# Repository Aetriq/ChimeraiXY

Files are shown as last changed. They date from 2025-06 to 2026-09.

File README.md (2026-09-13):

# Chimera iXY - CoreXY Build

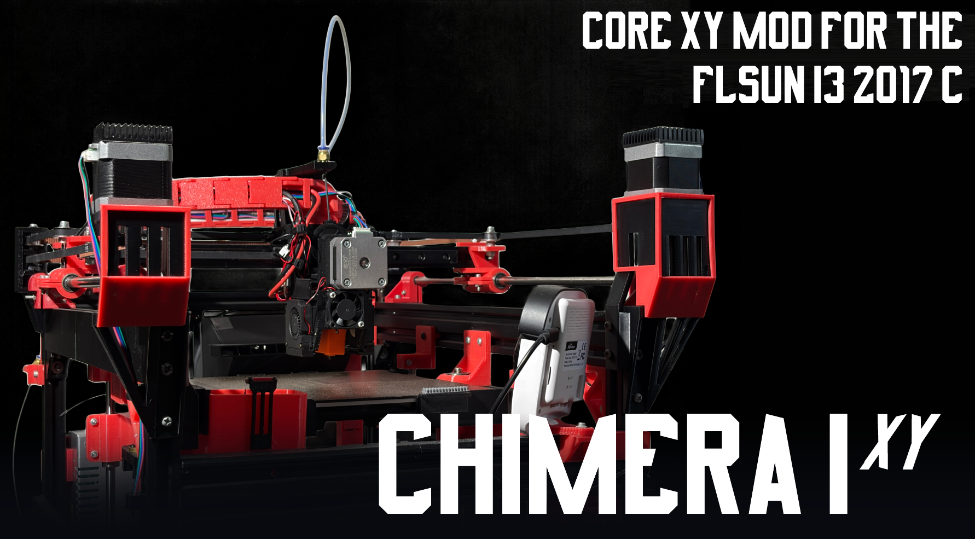
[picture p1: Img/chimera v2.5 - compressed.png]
Banner 1

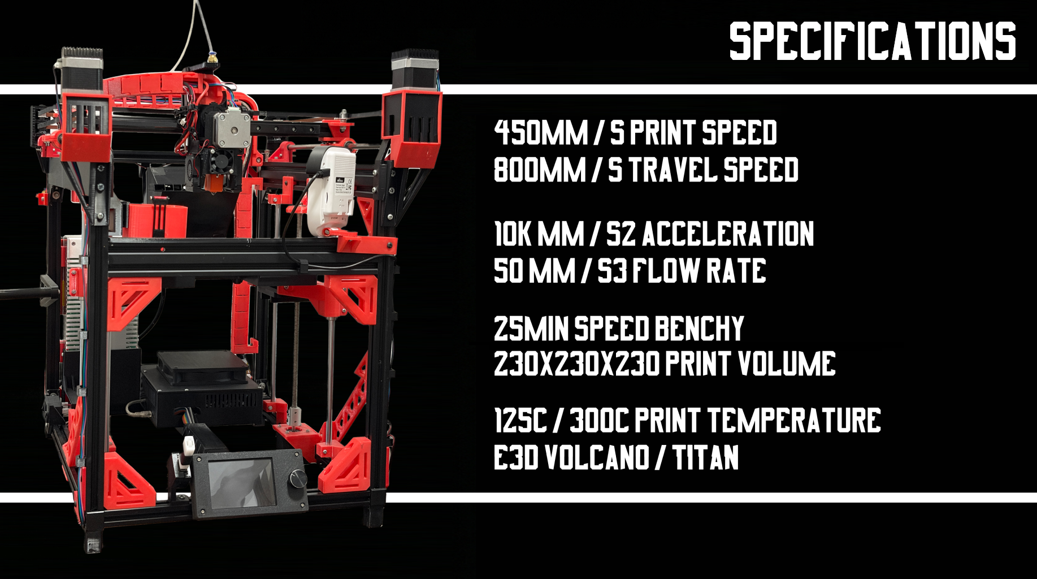
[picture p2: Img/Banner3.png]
Banner 2


A DIY CoreXY conversion of the Flsun i3 2017 3D printer. This project includes firmware and relevant 3D model files for the custom build. A Mingda Magician X with a burnt out mainboard and 20-pin ribbon cable was also used in this build. I chose the name 'Chimera' since this printer is essentially two completely different 3D printers with a ~5 year gap combined together to make a hybrid printer.

This is not only to demonstrate the ability of upcycling reprap in conjunction with modern printers, but also to prove that only linear rods, bearings and extrusions are needed to make a fast printer that rivals high end consumer printers while being at a lower cost.

**What's the objective of this project?** My main objective is not to make an insanely fast 3D printer, anything above 200mm/s is the goal with speeds near 500mm/s in mind. Instead, I wanted to make this printer as reliable as possible, moreso than the two bedslingers it was made out of. The Flsun (While a good printer for its time) is obviously last gen, so it's quite finicky to get quality models by today's standards, and the MMX was simply made out of cheap parts that probably didn't even pass QoS (there's also alot of review online of mingda printers using parts with questionable quality). This printer will primarily be used to build large electronic enclosures. 

**LATEST UPDATE LOG (v2.4):** - Added a nozzle cleaning system, including a ptfe wiper and nozzle brush. Partially inspired by the system seen on bambu's a1 series, this system works very well and the klipper config has been updated accordingly.
- Added an auxillary cooling fan, a 120x25mm axial 150CFM fan. This should've been a centrifugal blower but I had this one on hand and it pushes a decent amount of H20 pressure.
- Quality of life improvements to firmware, including the implementation of above. Thermal testing of steppers made me stay at 1.2A RMS for X and Y motors.

## Overview of Specifications

- **Firmware**: Klipper & MainsailOS. Marlin 2.1.2.5 continues to be supported.  
- **Controller Board**: Supports MKS Gen L vX.X, TinyBee vX.X, and Robin Nano v3.X.*
- **Build Type**: CoreXY mechanical configuration
- **Speed**: Quality Prints @ 300mm/s. Travel speeds up to 800mm/s.
- **Accel**: Up to 20k mm/s*s accel
- **Drivers**: Minimum TMC2209 UART required (>2.0A peak)
- **Build Volume**: 230mm^3
- **Extrusion**: E3D Titan Extruder Direct Drive or Bowden.
- **Hotend**: V6 volcano or normal w/ all-metal heatbreak. Supports PLA, PETG, ABS, ASA, TPU (>72D)

**Due to unforeseen circumstances, I have changed to the Robin Nano v3.1.* ### Experimental Results
Below is a comparison of the donor hardware versus the theoretical goals and final experimental data. In conclusion, alot of my project goals were met and even exceeded in some cases!

| Specification | Flsun i3 (Donor 1) | Mingda Magician X (Donor 2) | Planned Theoretical Goal | Experimental Results |
| :--- | :--- | :--- | :--- | :--- |
| **Max Print Speed** | ~100 mm/s | ~80-120 mm/s | 200-500 mm/s | 200-450mm/s|
| **Max Travel Speed** | ~150 mm/s | ~200 mm/s | 500+ mm/s | 800mm/s |
| **Max Acceleration** | ~1000 mm/s² | ~1500 mm/s² | 20000 mm/s² | 32000 mm/s² (according to input shaping)|
| **Volumetric Flow Rate** | ~8 mm³/s | ~10-12 mm³/s | >20 mm³/s | 40 mm³/s|
| **Build Volume** | 220x220x220 mm | 230x230x260 mm | 230x230x230 mm | 230x230x230 mm|
| **Kinematics** | Cartesian | Cartesian | CoreXY | CoreXY |

## Links

- [Official Page](https://aetriq.xyz/chimera.html)
- [Wiki Page](https://github.com/Aetriq/ChimeraiXY/wiki/Wiki-Page-%E2%80%90-Chimera-iXY-v2.0)
- [Full Documentation](https://aetriq.xyz/chimeradocfull.html)
- [Bill of Materials](https://aetriq.xyz/chimeradocfull.html#bom)

## Contents

- `Firmware - Mainboard/` – Klipper & Marlin 2.1.2.5 configuration for MKS Robin Nano v3.1. 
- `Firmware - ESP8266/` – Configuration for MKS Wifi v1.0. Only used in Marlin Build. 
- `Config/` - Slicer Profiles, Bootscreen, etc.
- `Model/` – 3D printable parts for CoreXY conversion (mounts, brackets, etc.)  
- `Doc/` – Rough Concept Sketches, Torque Curves, and printer setup details
- `Img/` – Images featured here, as well as some diagrams

## Configuration
Refer to config folder for start gcode for marlin, or firmware for klipper start/end gcode. This printer works optimally on both superslicer or prusaslicer but supports any marlin flavored gcode.

## Model Credits
Credits to the following models for making this possible. Please check them out:

- [1] 20 x 20 mm extrusion Power Source Unit (PSU) mount bracket – [[source/link](https://www.printables.com/model/457450-20-x-20-mm-extrusion-power-source-unit-psu-mount-b/files)]  
- [2] Bowden / PTFE Tube Coupler - Connect 2 Tubes – [[source/link](https://makerworld.com/en/models/664607-bowden-ptfe-tube-coupler-connect-2-tubes#profileId-591977)]  
- [3] E3D v6 dual 4010 fan duct – [[source/link](https://www.printables.com/model/239901-e3d-v6-dual-4010-fan-duct/files)]  
- [4] the100: 8mm linear rod gantry - [[source/link](https://github.com/MSzturc/the100/tree/main/STL/Gantry)]
- [5] KP3S PSU 120mm fan adapter (ZL-360-24) - [[source/link](https://www.thingiverse.com/thing:6010144)]
- [6] Case for Makerbase MKS TS35 V2.0 touchscreen - [[source/link](https://www.printables.com/model/83429-case-for-makerbase-mks-ts35-v20-touchscreen/comments)]
- [7] Drag Cable Chain(s) - [[source/link](https://www.printables.com/model/34894-drag-cable-chains/files)]
- [8] Modification pack, Ender 5 plus, KAY3D CoreXY. - [[source/link](https://www.thingiverse.com/thing:4643208/files)]

## Software Credits
- [1] Autodesk Fusion [[source/link](https://www.autodesk.com/products/fusion-360/personal)]
- [2] PrusaSlicer [[source/link](https://www.prusa3d.com/page/prusaslicer_424/)]
- [3] SuperSlicer [[source/link](https://superslicer.net/)]
- [4] Klipper [[source/link](https://www.klipper3d.org/)]
- [5] Configuration for MKS TS35 V2.0 working with klipper screen [[source/link](https://github.com/NamkingWIN/3d_print/wiki/Configuration-for-MKS-TS35-V2.0-working-with-klipper-screen)]
- [6] StepperSim [[source/link](https://github.com/rcarlyle/StepperSim)]

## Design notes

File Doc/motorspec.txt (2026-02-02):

42SHDC4023Z-23B

- 17 Stepper
- 42 Motor
- Step angle: 1.8 degree
- Number of phases: 2
- Voltage: DC 2.55V
- Current: 1.5A/phase
- Resistance: 4.4 ohm
- Holding torque: 2420 mN.m
- Positioning torque : 20mN.m REF

 42BYGH439-B-20D
- 17 Stepper
- 42 Motor
- Step angle: Likely 0.9 degree
- Number of phases: 2
- Voltage: DC 2.55V
- Current: 1.7A/Phase
- Resistance: 1.5-1.8 ohm
- Holding torque: ~40 - 45 N.cm

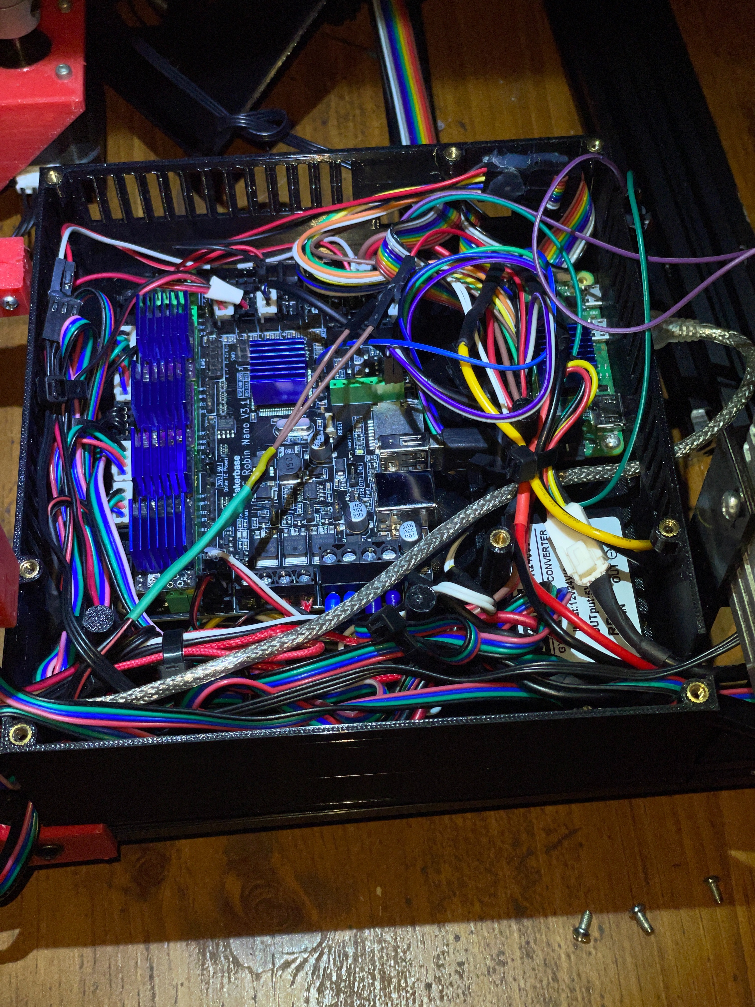
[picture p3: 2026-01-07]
Img/Primary Electronics Case.JPG

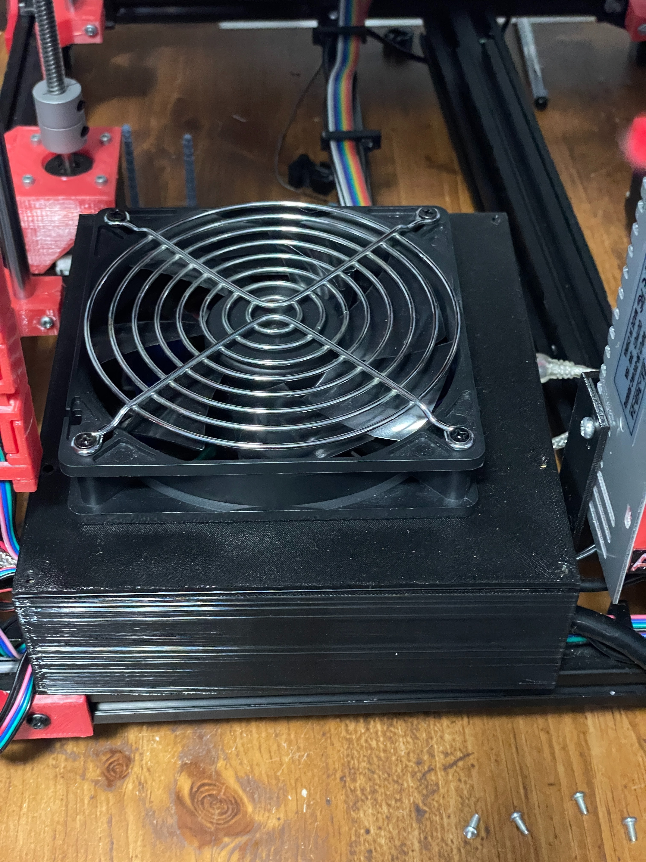
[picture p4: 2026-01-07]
Img/Primary Electronics Case Closed.JPG

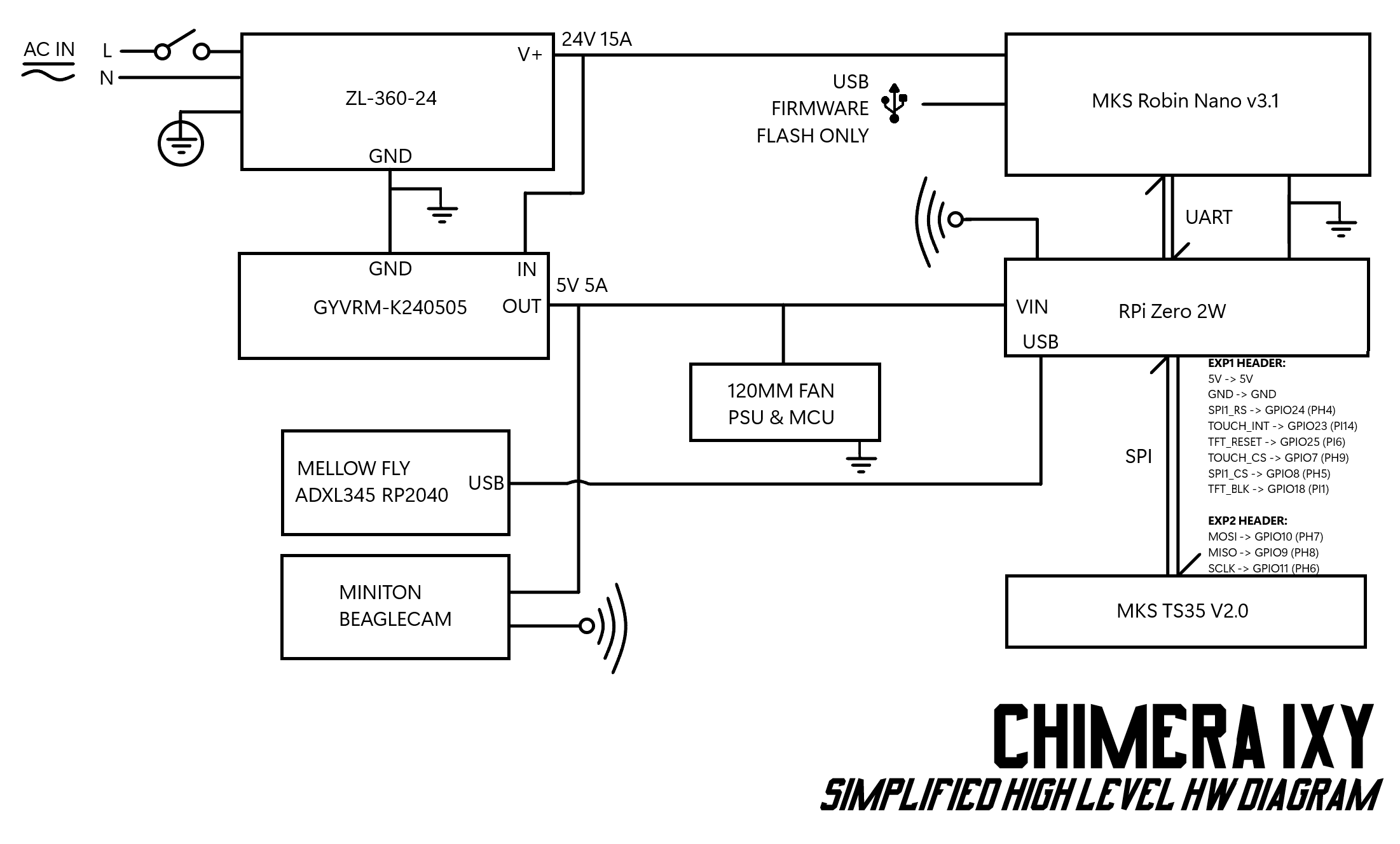
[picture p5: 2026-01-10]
Doc/Simplified Hardware Diagram.png

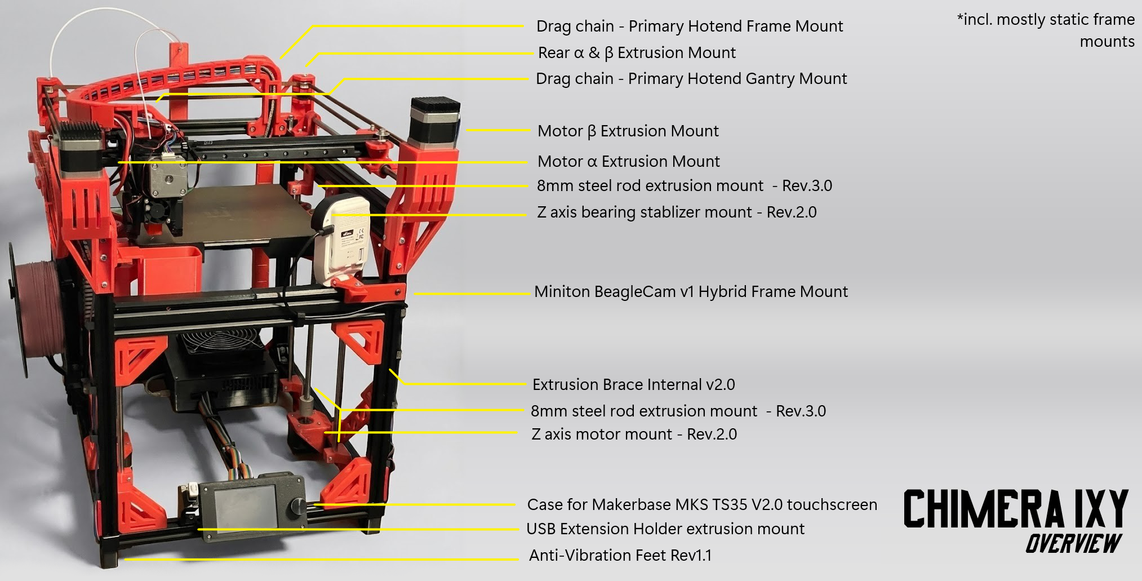
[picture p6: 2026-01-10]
Doc/Overview v2.0.png

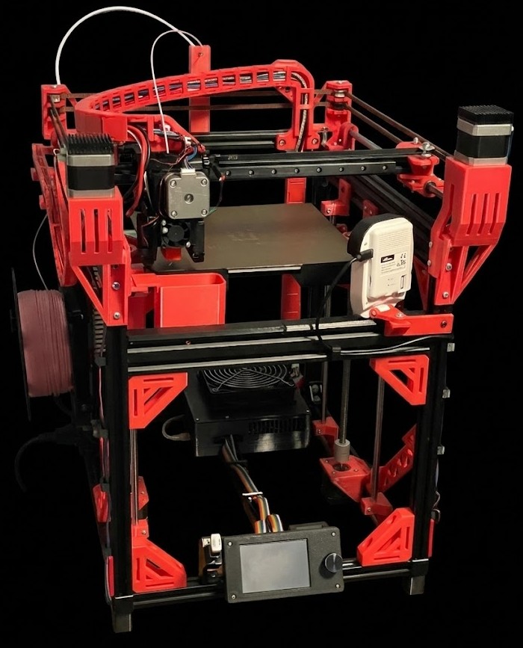
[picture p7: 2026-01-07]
Img/v2.0.jpg

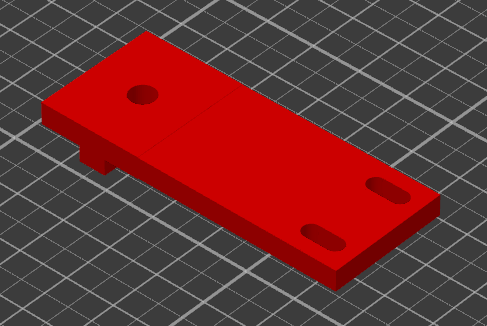
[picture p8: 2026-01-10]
Img/thumb/Y axis endstop switch Frame Mount.png

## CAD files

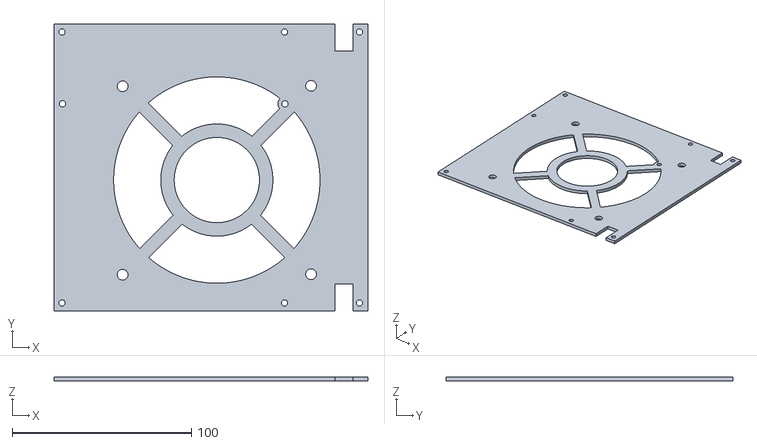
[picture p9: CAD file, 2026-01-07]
Model/Electronics/Primary Case - Top Cover.stl
175.0 x 160.0 x 2.50

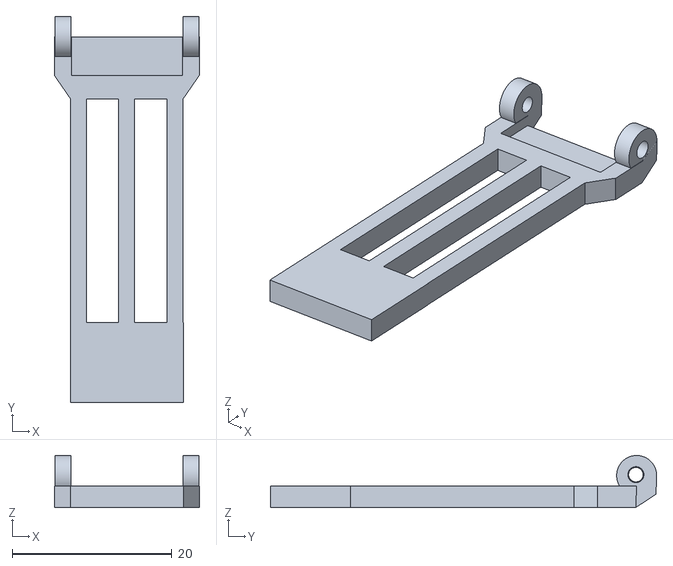
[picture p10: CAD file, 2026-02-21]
Model/etc/Glue-on PTFE Nozzle Wiper.stl
18.1 x 48.3 x 6.51

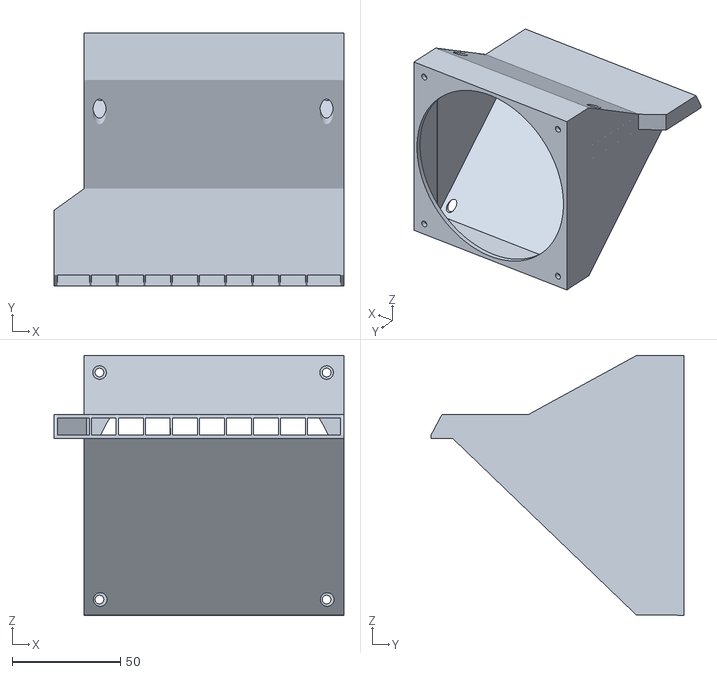
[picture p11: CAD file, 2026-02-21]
Model/Frame Mounts/Auxillary Bed Cooling Fan Mount (120mm Axial, mirror other side) (2).stl
134.1 x 117.0 x 120.3

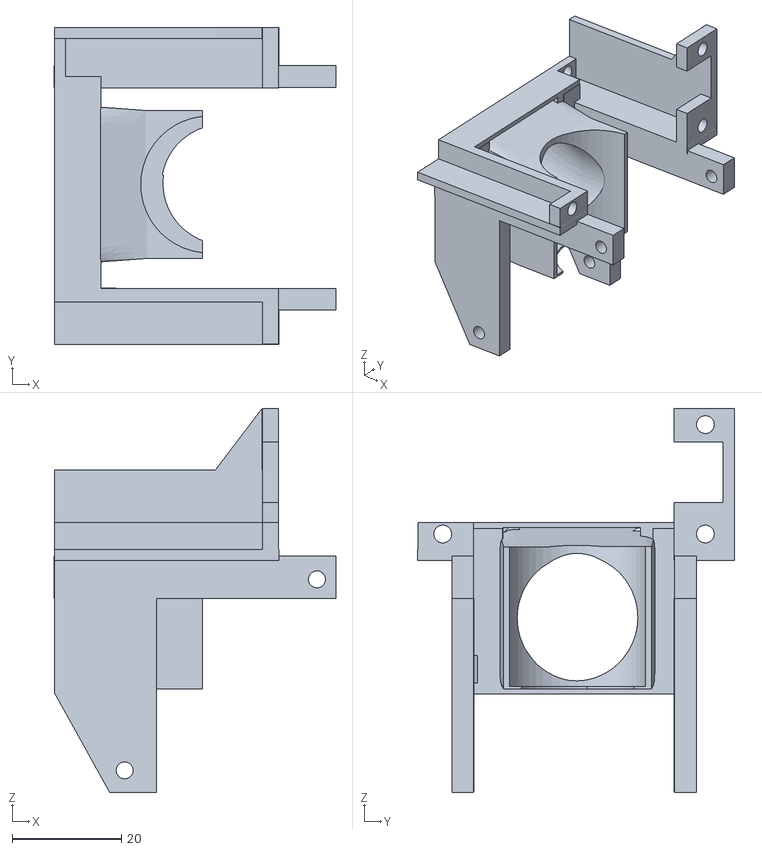
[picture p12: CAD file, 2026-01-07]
Model/Gantry/Mounting Bracket - Fans.stl
51.5 x 57.9 x 70.2

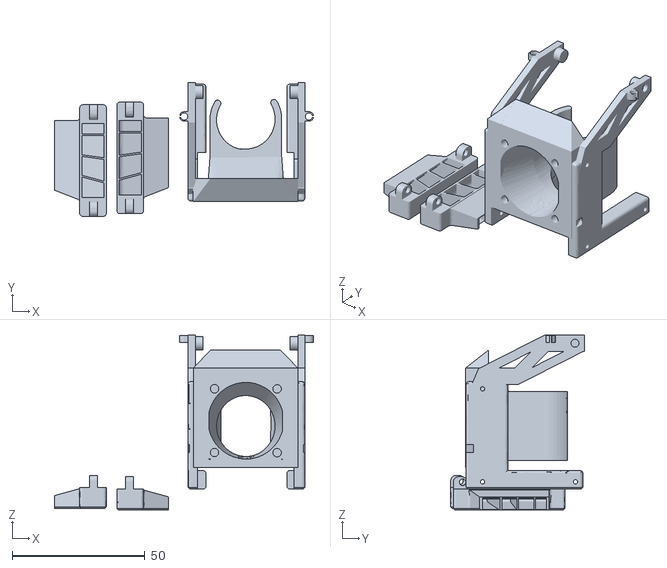
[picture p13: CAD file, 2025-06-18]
Model/Hotend/Hotend 30mm + 4010x2 Shroud.stl
97.5 x 50.3 x 65.7

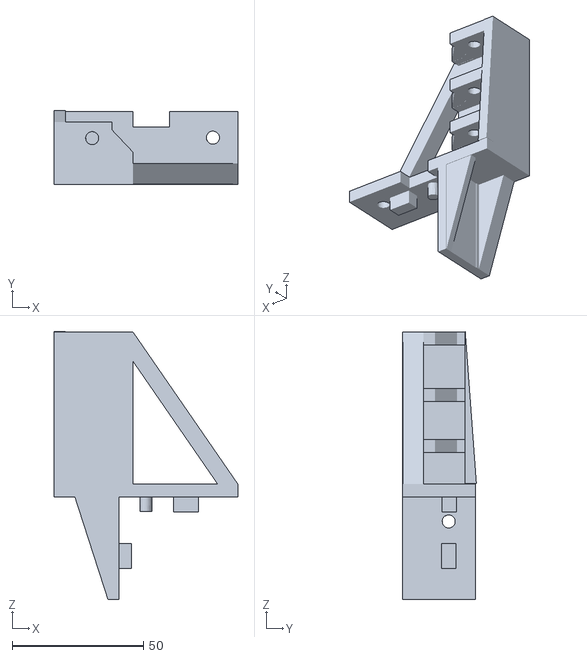
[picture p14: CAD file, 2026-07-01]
Model/Kinematics/Rear α & β Extrusion Mount (Right side, mirror model on y for left side) v2.5.stl
70.0 x 28.1 x 102.1

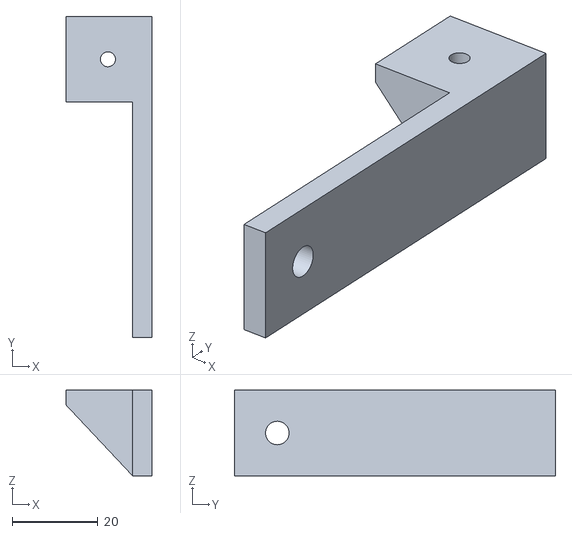
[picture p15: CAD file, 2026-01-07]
Model/Electronics/Miniton BeagleCam v1 Hybrid Frame Mount.stl
20.0 x 75.0 x 20.0

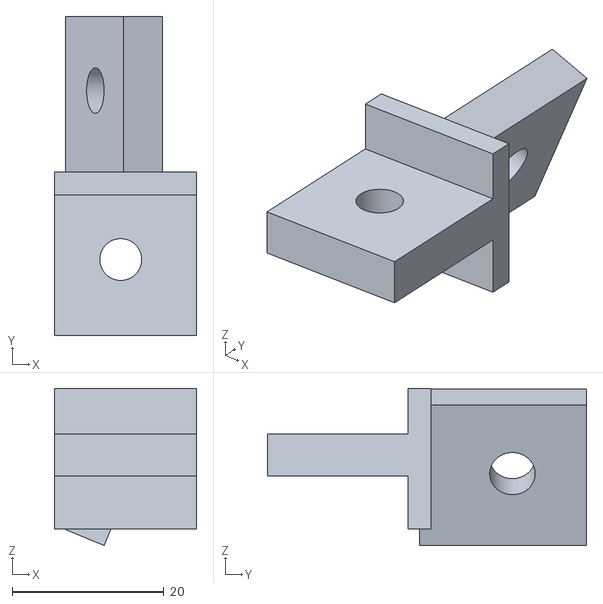
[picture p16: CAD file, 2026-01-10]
Model/etc/Filament Guide - Bottom.stl
18.8 x 42.0 x 20.7

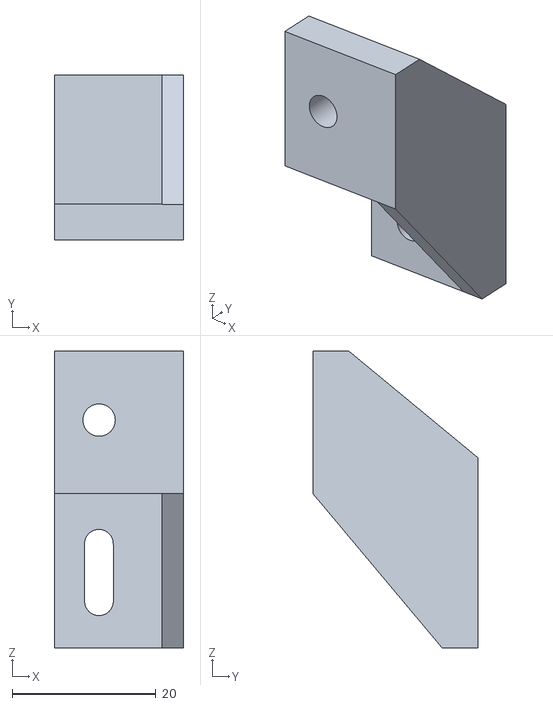
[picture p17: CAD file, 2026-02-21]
Model/Frame Mounts/Auxillary Bed Cooling Fan Mount (120mm Axial, mirror other side) (1).stl
18.0 x 23.0 x 41.4

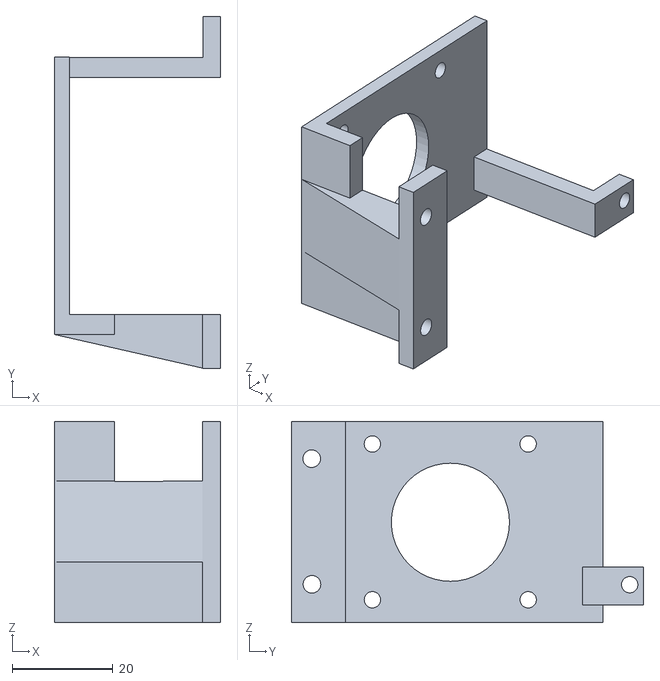
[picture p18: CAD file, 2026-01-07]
Model/Gantry/Mounting Bracket - Extruder & Hotend.stl
33.1 x 70.1 x 40.0

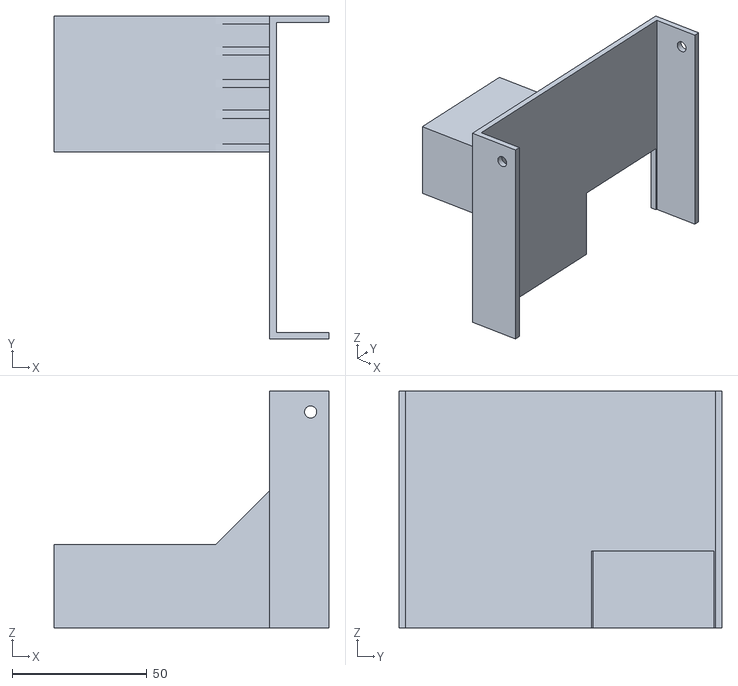
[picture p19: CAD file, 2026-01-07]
Model/Electronics/Power Supply Cover.stl
102.0 x 120.0 x 88.0

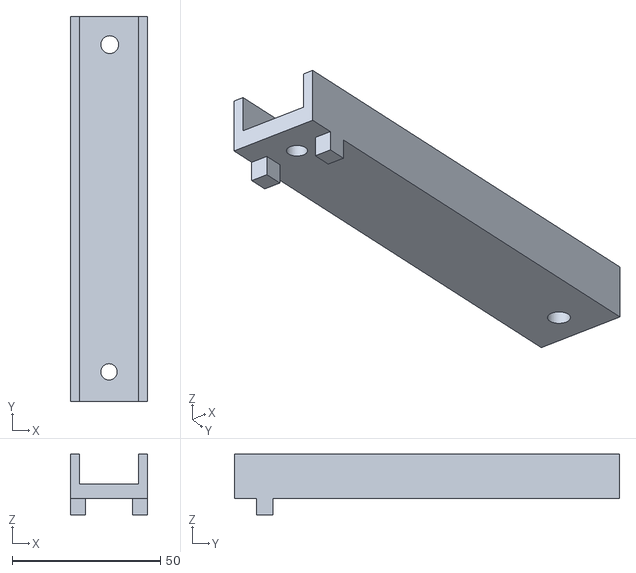
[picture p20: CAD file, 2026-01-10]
Model/etc/Filament Guide - Top.stl
26.0 x 130.0 x 20.5

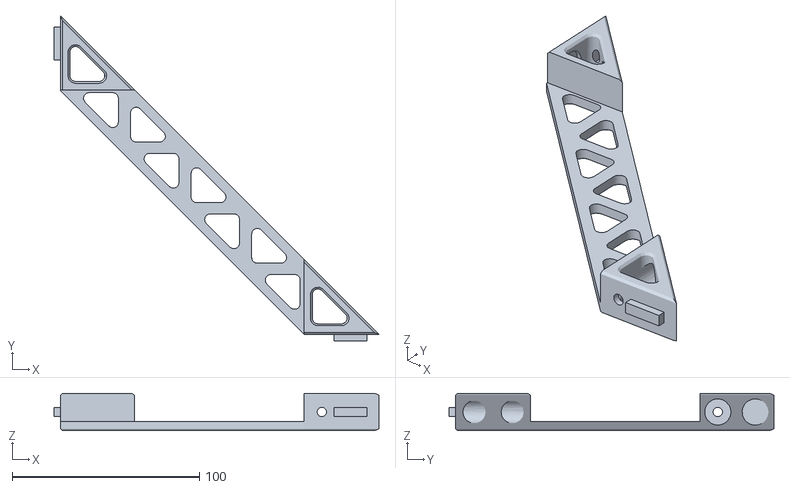
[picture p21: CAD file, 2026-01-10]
Model/Frame Mounts/Extrusion Brace Internal Long.stl
173.5 x 173.5 x 20.0

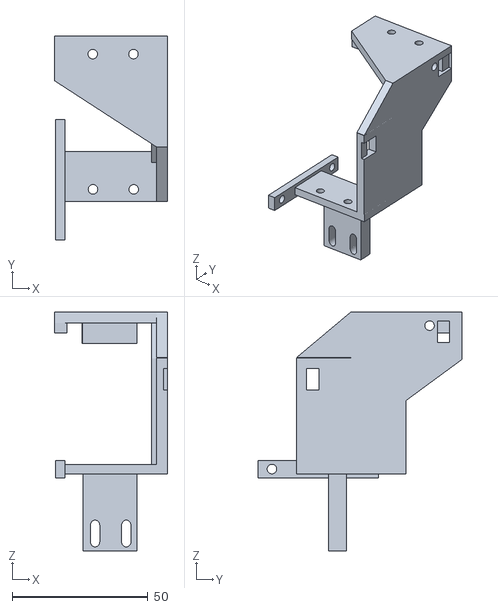
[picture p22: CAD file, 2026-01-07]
Model/Gantry/Back Gantry Plate.stl
41.7 x 75.0 x 87.9

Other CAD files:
Model/Electronics/Primary Case - Bottom.stl
Model/etc/Filament Spool Holder v2.0 Part 1.stl
Model/Frame Mounts/8mm steel rod extrusion mount (Z-axis, Bottom & Top) - Rev.3.0.stl
Model/Gantry/4010 Shroud.stl
Model/Electronics/MKS TFT35 v2.0 Extrusion Mount (Modified).stl
Model/Frame Mounts/15mm square tube cable clip (Epoxy Mounted).stl
Model/Frame Mounts/15mm square tube extrusion mount.stl
Model/Frame Mounts/30mm height psu support.stl
Model/Frame Mounts/8mm steel rod extrusion mount (OLD).stl
Model/Frame Mounts/8mm steel rod extrusion mount (Y-axis) - Rev.1.0.stl
Model/Frame Mounts/AC Plug + Power Switch extrusion mount.stl
Model/Frame Mounts/Anti-Vibration Feet Rev1.1.stl
Model/Frame Mounts/Cable guide extrusion mount (OLD).stl
Model/Frame Mounts/Cable guide extrusion mount.stl
Model/Frame Mounts/Drag chain - Auxillary Rear Spine Mount.stl
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

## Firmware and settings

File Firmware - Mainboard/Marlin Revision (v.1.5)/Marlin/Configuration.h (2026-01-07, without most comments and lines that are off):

#pragma once
#define CONFIGURATION_H_VERSION 02010205
#define STRING_CONFIG_H_AUTHOR "(none, default config)" // Who made the changes.
#define SHOW_BOOTSCREEN
  #define MOTHERBOARD BOARD_MKS_ROBIN_NANO_V3
#define SERIAL_PORT -1
#define BAUDRATE 250000
#define CUSTOM_MACHINE_NAME "Chimera iXY"
#define X_DRIVER_TYPE  TMC2209
#define Y_DRIVER_TYPE  TMC2209
#define Z_DRIVER_TYPE  TMC2209_STANDALONE
#define E0_DRIVER_TYPE TMC2209_STANDALONE
#define EXTRUDERS 1
#define DEFAULT_NOMINAL_FILAMENT_DIA 1.75
#define TEMP_SENSOR_0 1
#define TEMP_SENSOR_1 0
#define TEMP_SENSOR_2 0
#define TEMP_SENSOR_3 0
#define TEMP_SENSOR_4 0
#define TEMP_SENSOR_5 0
#define TEMP_SENSOR_6 0
#define TEMP_SENSOR_7 0
#define TEMP_SENSOR_BED 1
#define TEMP_SENSOR_PROBE 0
#define TEMP_SENSOR_CHAMBER 0
#define TEMP_SENSOR_COOLER 0
#define TEMP_SENSOR_BOARD 0
#define TEMP_SENSOR_REDUNDANT 0
#define DUMMY_THERMISTOR_998_VALUE  25
#define DUMMY_THERMISTOR_999_VALUE 100
#if TEMP_SENSOR_IS_MAX_TC(0)
  #define MAX31865_SENSOR_OHMS_0      100 // (Ω) Typically 100 or 1000 (PT100 or PT1000)
  #define MAX31865_CALIBRATION_OHMS_0 430 // (Ω) Typically 430 for Adafruit PT100; 4300 for Adafruit PT1000
#endif
#if TEMP_SENSOR_IS_MAX_TC(1)
  #define MAX31865_SENSOR_OHMS_1      100
  #define MAX31865_CALIBRATION_OHMS_1 430
#endif
#if TEMP_SENSOR_IS_MAX_TC(2)
  #define MAX31865_SENSOR_OHMS_2      100
  #define MAX31865_CALIBRATION_OHMS_2 430
#endif
#if HAS_E_TEMP_SENSOR
  #define TEMP_RESIDENCY_TIME         5  // (seconds) Time to wait for hotend to "settle" in M109
  #define TEMP_WINDOW                  1  // (°C) Temperature proximity for the "temperature reached" timer
  #define TEMP_HYSTERESIS              3  // (°C) Temperature proximity considered "close enough" to the target
#endif
#if TEMP_SENSOR_BED
  #define TEMP_BED_RESIDENCY_TIME     5  // (seconds) Time to wait for bed to "settle" in M190
  #define TEMP_BED_WINDOW              1  // (°C) Temperature proximity for the "temperature reached" timer
  #define TEMP_BED_HYSTERESIS          3  // (°C) Temperature proximity considered "close enough" to the target
#endif
#if TEMP_SENSOR_CHAMBER
  #define TEMP_CHAMBER_RESIDENCY_TIME 10  // (seconds) Time to wait for chamber to "settle" in M191
  #define TEMP_CHAMBER_WINDOW          1  // (°C) Temperature proximity for the "temperature reached" timer
  #define TEMP_CHAMBER_HYSTERESIS      3  // (°C) Temperature proximity considered "close enough" to the target
#endif
#if TEMP_SENSOR_REDUNDANT
  #define TEMP_SENSOR_REDUNDANT_SOURCE    E1  // The sensor that will provide the redundant reading.
  #define TEMP_SENSOR_REDUNDANT_TARGET    E0  // The sensor that we are providing a redundant reading for.
  #define TEMP_SENSOR_REDUNDANT_MAX_DIFF  10  // (°C) Temperature difference that will trigger a print abort.
#endif
#define HEATER_0_MINTEMP   5
#define HEATER_1_MINTEMP   5
#define HEATER_2_MINTEMP   5
#define HEATER_3_MINTEMP   5
#define HEATER_4_MINTEMP   5
#define HEATER_5_MINTEMP   5
#define HEATER_6_MINTEMP   5
#define HEATER_7_MINTEMP   5
#define BED_MINTEMP        5
#define CHAMBER_MINTEMP    5
#define HEATER_0_MAXTEMP 275
#define HEATER_1_MAXTEMP 275
#define HEATER_2_MAXTEMP 275
#define HEATER_3_MAXTEMP 275
#define HEATER_4_MAXTEMP 275
#define HEATER_5_MAXTEMP 275
#define HEATER_6_MAXTEMP 275
#define HEATER_7_MAXTEMP 275
#define BED_MAXTEMP      150
#define CHAMBER_MAXTEMP  60
#define HOTEND_OVERSHOOT 15   // (°C) Forbid temperatures over MAXTEMP - OVERSHOOT
#define BED_OVERSHOOT    10   // (°C) Forbid temperatures over MAXTEMP - OVERSHOOT
#define COOLER_OVERSHOOT  2   // (°C) Forbid temperatures closer than OVERSHOOT
#define PIDTEMP           // See the PID Tuning Guide at https://reprap.org/wiki/PID_Tuning
#define PID_MAX  255      // Limit hotend current while PID is active (see PID_FUNCTIONAL_RANGE below); 255=full current
#define PID_K1     0.95   // Smoothing factor within any PID loop
    #define DEFAULT_Kp  22.20
    #define DEFAULT_Ki   1.08
    #define DEFAULT_Kd 114.00
#define MAX_BED_POWER 255 // limits duty cycle to bed; 255=full current
#define MAX_CHAMBER_POWER 255 // limits duty cycle to chamber heater; 255=full current
  #define PID_FUNCTIONAL_RANGE 10 // If the temperature difference between the target temperature and the actual temperature
#define PREVENT_COLD_EXTRUSION
#define EXTRUDE_MINTEMP 170
#define PREVENT_LENGTHY_EXTRUDE
#define EXTRUDE_MAXLENGTH 200
#define THERMAL_PROTECTION_HOTENDS // Enable thermal protection for all extruders
#define THERMAL_PROTECTION_BED     // Enable thermal protection for the heated bed
#define THERMAL_PROTECTION_CHAMBER // Enable thermal protection for the heated chamber
#define THERMAL_PROTECTION_COOLER  // Enable thermal protection for the laser cooling
#define COREXY
#define USE_XMIN_PLUG
#define USE_YMIN_PLUG
#define USE_ZMIN_PLUG
#define ENDSTOPPULLUPS
#define X_MIN_ENDSTOP_INVERTING false // Set to true to invert the logic of the endstop.
#define Y_MIN_ENDSTOP_INVERTING true // Set to true to invert the logic of the endstop.
#define Z_MIN_ENDSTOP_INVERTING true // Set to true to invert the logic of the endstop.
#define I_MIN_ENDSTOP_INVERTING false // Set to true to invert the logic of the endstop.
#define J_MIN_ENDSTOP_INVERTING false // Set to true to invert the logic of the endstop.
#define K_MIN_ENDSTOP_INVERTING false // Set to true to invert the logic of the endstop.
#define U_MIN_ENDSTOP_INVERTING false // Set to true to invert the logic of the endstop.
#define V_MIN_ENDSTOP_INVERTING false // Set to true to invert the logic of the endstop.
#define W_MIN_ENDSTOP_INVERTING false // Set to true to invert the logic of the endstop.
#define X_MAX_ENDSTOP_INVERTING false // Set to true to invert the logic of the endstop.
#define Y_MAX_ENDSTOP_INVERTING false // Set to true to invert the logic of the endstop.
#define Z_MAX_ENDSTOP_INVERTING false // Set to true to invert the logic of the endstop.
#define I_MAX_ENDSTOP_INVERTING false // Set to true to invert the logic of the endstop.
#define J_MAX_ENDSTOP_INVERTING false // Set to true to invert the logic of the endstop.
#define K_MAX_ENDSTOP_INVERTING false // Set to true to invert the logic of the endstop.
#define U_MAX_ENDSTOP_INVERTING false // Set to true to invert the logic of the endstop.
#define V_MAX_ENDSTOP_INVERTING false // Set to true to invert the logic of the endstop.
#define W_MAX_ENDSTOP_INVERTING false // Set to true to invert the logic of the endstop.
#define Z_MIN_PROBE_ENDSTOP_INVERTING true // Set to true to invert the logic of the probe.
#define DEFAULT_AXIS_STEPS_PER_UNIT   { 100, 100, 100, 167 }
#define DEFAULT_MAX_FEEDRATE          { 300, 300, 5, 25 }
#define DEFAULT_MAX_ACCELERATION      { 3000, 3000, 100, 10000 }
#define DEFAULT_ACCELERATION          3000    // X, Y, Z and E acceleration for printing moves
#define DEFAULT_RETRACT_ACCELERATION  3000    // E acceleration for retracts
#define DEFAULT_TRAVEL_ACCELERATION   3000    // X, Y, Z acceleration for travel (non printing) moves
#define DEFAULT_EJERK    5.0  // May be used by Linear Advance
  #define JUNCTION_DEVIATION_MM 0.013 // (mm) Distance from real junction edge
  #define JD_HANDLE_SMALL_SEGMENTS    // Use curvature estimation instead of just the junction angle
#define Z_MIN_PROBE_USES_Z_MIN_ENDSTOP_PIN
#define USE_PROBE_FOR_Z_HOMING
#define FIX_MOUNTED_PROBE
#define NOZZLE_TO_PROBE_OFFSET { 0, -60, 0 }
#define PROBING_MARGIN 10
#define XY_PROBE_FEEDRATE (133*60)
#define Z_PROBE_FEEDRATE_FAST (4*60)
#define Z_PROBE_FEEDRATE_SLOW (Z_PROBE_FEEDRATE_FAST / 2)
#define Z_CLEARANCE_DEPLOY_PROBE   10 // (mm) Z Clearance for Deploy/Stow
#define Z_CLEARANCE_BETWEEN_PROBES  5 // (mm) Z Clearance between probe points
#define Z_CLEARANCE_MULTI_PROBE     5 // (mm) Z Clearance between multiple probes
#define Z_PROBE_LOW_POINT          -2 // (mm) Farthest distance below the trigger-point to go before stopping
#define Z_PROBE_OFFSET_RANGE_MIN -20
#define Z_PROBE_OFFSET_RANGE_MAX 20
#define X_ENABLE_ON 0
#define Y_ENABLE_ON 0
#define Z_ENABLE_ON 0
#define E_ENABLE_ON 0 // For all extruders
#define DISABLE_OTHER_EXTRUDERS   // Keep only the active extruder enabled
#define INVERT_X_DIR false
#define INVERT_Y_DIR false
#define INVERT_Z_DIR true
#define INVERT_E0_DIR true
#define INVERT_E1_DIR false
#define INVERT_E2_DIR false
#define INVERT_E3_DIR false
#define INVERT_E4_DIR false
#define INVERT_E5_DIR false
#define INVERT_E6_DIR false
#define INVERT_E7_DIR false
#define X_HOME_DIR -1
#define Y_HOME_DIR -1
#define Z_HOME_DIR -1
#define X_BED_SIZE 230
#define Y_BED_SIZE 230
#define X_MIN_POS 0
#define Y_MIN_POS 0
#define Z_MIN_POS 0
#define X_MAX_POS X_BED_SIZE
#define Y_MAX_POS Y_BED_SIZE
#define Z_MAX_POS 200
#define MIN_SOFTWARE_ENDSTOPS
  #define MIN_SOFTWARE_ENDSTOP_X
  #define MIN_SOFTWARE_ENDSTOP_Y
  #define MIN_SOFTWARE_ENDSTOP_Z
  #define MIN_SOFTWARE_ENDSTOP_I
  #define MIN_SOFTWARE_ENDSTOP_J
  #define MIN_SOFTWARE_ENDSTOP_K
  #define MIN_SOFTWARE_ENDSTOP_U
  #define MIN_SOFTWARE_ENDSTOP_V
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

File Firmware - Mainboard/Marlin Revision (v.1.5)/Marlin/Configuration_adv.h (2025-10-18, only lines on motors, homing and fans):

#define E0_AUTO_FAN_PIN PB1
#define E1_AUTO_FAN_PIN -1
#define E2_AUTO_FAN_PIN -1
#define E3_AUTO_FAN_PIN -1
#define E4_AUTO_FAN_PIN -1
#define E5_AUTO_FAN_PIN -1
#define E6_AUTO_FAN_PIN -1
#define E7_AUTO_FAN_PIN -1
#define CHAMBER_AUTO_FAN_PIN -1
#define COOLER_AUTO_FAN_PIN -1
#define HOMING_BUMP_MM      { 5, 5, 2 }       // (linear=mm, rotational=°) Backoff from endstops after first bump
#define HOMING_BUMP_DIVISOR { 2, 2, 4 }       // Re-Bump Speed Divisor (Divides the Homing Feedrate)
#define MICROSTEP_MODES { 16, 16, 16, 16, 16, 16 } // [1,2,4,8,16]
#define LIN_ADVANCE
    #define ADVANCE_K 0.22        // (mm) Compression length applying to all extruders
    #define X_CURRENT       800        // (mA) RMS current. Multiply by 1.414 for peak current.
    #define X_CURRENT_HOME  X_CURRENT  // (mA) RMS current for homing. (Typically lower than *_CURRENT.)
    #define X_MICROSTEPS     16        // 0..256
    #define Y_CURRENT       800
    #define Y_CURRENT_HOME  Y_CURRENT
    #define Y_MICROSTEPS     16
  #define HYBRID_THRESHOLD
  #define X_HYBRID_THRESHOLD     100  // [mm/s]
  #define X2_HYBRID_THRESHOLD    100
  #define Y_HYBRID_THRESHOLD     100
  #define Y2_HYBRID_THRESHOLD    100
  #define Z_HYBRID_THRESHOLD       5
  #define Z2_HYBRID_THRESHOLD      3
  #define Z3_HYBRID_THRESHOLD      3
  #define Z4_HYBRID_THRESHOLD      3
  #define I_HYBRID_THRESHOLD       3  // [linear=mm/s, rotational=°/s]
  #define J_HYBRID_THRESHOLD       3  // [linear=mm/s, rotational=°/s]
  #define K_HYBRID_THRESHOLD       3  // [linear=mm/s, rotational=°/s]
  #define U_HYBRID_THRESHOLD       3  // [mm/s]
  #define V_HYBRID_THRESHOLD       3
  #define W_HYBRID_THRESHOLD       3
  #define E0_HYBRID_THRESHOLD     30
  #define E1_HYBRID_THRESHOLD     30
  #define E2_HYBRID_THRESHOLD     30
  #define E3_HYBRID_THRESHOLD     30
  #define E4_HYBRID_THRESHOLD     30
  #define E5_HYBRID_THRESHOLD     30
  #define E6_HYBRID_THRESHOLD     30
  #define E7_HYBRID_THRESHOLD     30

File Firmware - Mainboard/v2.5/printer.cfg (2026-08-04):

# Chimera iXY v2.5 - Klipper Configuration Revision 1.5
# General Setup: 
  # CoreXY Kinematics
  # MKS Robin Nano V3.1 + MKS TS35 v2.0
  # RPi Zero 2W + Mellow Fly RP2040
  # TMC2209 Drivers (UART X/Y, STANDALONE E/Z)
  # Titan Extruder + V6 Volcano
# Last updated: 8-4-26

[include mainsail.cfg]
[include accelerometer.cfg]

[mcu]
serial: /dev/ttyAMA0
restart_method: command

[printer]
kinematics: corexy
max_velocity: 450
max_accel: 6400
max_z_velocity: 8
max_z_accel: 50

[virtual_sdcard]
path: /home/chimera/printer_data/gcodes
on_error_gcode: CANCEL_PRINT

#####################################################################
#      X/Y Stepper Settings
#####################################################################

[stepper_x]
step_pin: PE0
dir_pin: PB9           
enable_pin: !PE1
rotation_distance: 32  
microsteps: 16
full_steps_per_rotation: 200
endstop_pin: ^PA15     
position_endstop: 0
position_max: 230
homing_speed: 65

[tmc2209 stepper_x]
uart_pin: PD7          
run_current: 1.200
stealthchop_threshold: 5

[stepper_y]
step_pin: PE3
dir_pin: PE2           
enable_pin: !PE4
rotation_distance: 32  
microsteps: 16
full_steps_per_rotation: 200
endstop_pin: ^!PD2    
position_endstop: 230 
position_max: 230
position_min: -80    
homing_speed: 65

[tmc2209 stepper_y]
uart_pin: PD5       
run_current: 1.200
stealthchop_threshold: 5

[input_shaper]
shaper_freq_x: 114.6
shaper_type_x: mzv
shaper_freq_y: 45.0
shaper_type_y: ei


#####################################################################
#      Z Stepper Settings
#####################################################################

[stepper_z]
step_pin: PB5
dir_pin: !PB4
enable_pin: !PB8
rotation_distance: 1
microsteps: 16
endstop_pin: probe:z_virtual_endstop
position_min: -5.0
position_max: 230
homing_speed: 7
second_homing_speed: 2

#####################################################################
#      Extruder
#####################################################################

[extruder]
step_pin: PD6
dir_pin: PD3
enable_pin: !PB3
rotation_distance: 1
microsteps: 16
nozzle_diameter: 0.800
filament_diameter: 1.750
heater_pin: PE5
sensor_type: Generic 3950
sensor_pin: PC1
min_temp: 0
max_temp: 450
max_extrude_only_distance: 200.0
max_extrude_cross_section: 4.0
pressure_advance: 0.035


#####################################################################
#      Bed Heater
#####################################################################

[heater_bed]
heater_pin: PA0
sensor_type: Generic 3950 
sensor_pin: PC0
min_temp: 0
max_temp: 150

#####################################################################
#      Probe & Mesh
#####################################################################

[probe]
pin: ^!PC8
x_offset: 4
y_offset: 40
speed: 3.0              
lift_speed: 8.0         
samples: 3             
samples_result: median   
sample_retract_dist: 2.0 
samples_tolerance: 0.02 
samples_tolerance_retries: 3

[safe_z_home]
home_xy_position: 115, 75 
speed: 50
z_hop: 10
z_hop_speed: 5

[bed_mesh]
speed: 200
horizontal_move_z: 5
mesh_min: 20, 20     
mesh_max: 210, 190   
probe_count: 6, 6
algorithm: bicubic

#####################################################################
#      Fans
#####################################################################

[fan]
pin: PC14

[heater_fan hotend_fan]
pin: PB1
heater: extruder
heater_temp: 50.0

[fan_generic auxiliary_fan]
pin: PB0 
max_power: 1.0
shutdown_speed: 0.0
kick_start_time: 0.5
off_below: 0.10          
cycle_time: 0.00004      
hardware_pwm: True   

#####################################################################
#      Macros
#####################################################################

[gcode_macro START_PRINT]
description: Custom start macro with nozzle cleaning sequence
gcode:
    {% set BED_TEMP = params.BED_TEMP|default(60)|float %}
    {% set EXTRUDER_TEMP = params.EXTRUDER_TEMP|default(190)|float %}
    {% set LAYER_HEIGHT = params.LAYER_HEIGHT|default(0.2)|float %}
    G28
    G90
    G1 Z10 F3000          
    G1 X20 Y-25 F4800    
    G1 Z3 F1000          
    M140 S{BED_TEMP}      
    M104 S{EXTRUDER_TEMP} 
    M109 S{EXTRUDER_TEMP} 
    G1 Z5 F1000         
    G1 Y-60 F12000        
    G1 X50 F1200          
    G1 X160 Y-8 F4800   
    G1 Z4 F1000          
    G1 X180 F12000
    G1 X160 F12000
    G1 X180 F12000
    G1 X160 F12000
    G1 X180 F12000
    G1 X160 F12000
    G1 X180 F12000
    G1 X160 F12000
    G1 X180 F12000
    G1 X160 F12000
    G1 Z10 F3000          
    G1 X20 Y-25 F4800     
    G92 E0             
    G1 E40 F300           
    G92 E0                
    M106 S255            
    G4 P3000             
    G1 Y-60 F12000        
    G1 X50 F1200          
    G1 Y-25 F1200          
    G1 X20 F1200          
    M106 S0               
    M190 S{BED_TEMP}    
    BED_MESH_PROFILE LOAD=mesh1
    G1 Y-60 F12000
    G1 X50 F3600 
    G1 Y5 F3600
    G92 E0.0
    G1 Z2.5 F3000
    G1 X5.0 Y5.0 Z{LAYER_HEIGHT} F5000.0
    G1 X5.0 Y55.0 Z{LAYER_HEIGHT} F1500.0 E10
    G1 X5.3 Y55.0 Z{LAYER_HEIGHT} F5000.0
    G1 X5.3 Y5.0 Z{LAYER_HEIGHT} F1500.0 E20
    G92 E0
    G1 E-1 F300
    G1 Z2.0 F3000

[gcode_macro END_PRINT]
gcode:
    G91                          
    G1 E-3 F300                  
    G1 Z10 F3000                  
    G90                           
    PARK_PURGE                   
    TURN_OFF_HEATERS
    M106 S0 
    SET_FAN_SPEED FAN=auxiliary_fan SPEED=0

#####################################################################
#      Filament Handling Macros
#####################################################################

[gcode_macro LOAD_FILAMENT]
gcode:
    {% set speed = params.SPEED|default(300) %}
    
    G91                 
    G92 E0
    G1 E30 F{speed}    
    G1 E30 F{speed}     
    G92 E0
    
    G90                   
    G1 X10 Y-25 F4800     
    G1 Y-60 F12000      
    
    G1 X50 F1200       
    G1 Y-25 F1200        
    G1 X10 F1200     

[gcode_macro UNLOAD_FILAMENT]
gcode:
    {% set speed = params.SPEED|default(300) %}
    G91                  
    G92 E0
    G1 E25 F{speed}       
    G1 E-100 F{speed}    
    G92 E0
    G90                  
    G1 X10 Y-25 F4800     
    G1 Y-60 F12000    
    G1 X50 F1200        
    G1 Y-25 F1200         
    G1 X10 F1200        

#####################################################################
#       Print State Management (Required for Pause/Resume)
#####################################################################

[pause_resume]

[display_status]

[gcode_macro PAUSE]
description: Pause the current print and store position
gcode:
    {% set velocity = printer.configfile.settings.printer.max_velocity %}
    G91 
    G1 Z10 F600 
    G90 
    M83 
    SAVE_GCODE_STATE NAME=PAUSE_STATE
    M117 Print Paused

[gcode_macro RESUME]
description: Resume the paused print
gcode:
    M117 Resuming Print
    RESTORE_GCODE_STATE NAME=PAUSE_STATE MOVE=1
    {% set hotend_temp = printer.lookup_object('extruder').target_temp %}
    {% set bed_temp = printer.lookup_object('heater_bed').target_temp %}
    M109 S{hotend_temp}
    M190 S{bed_temp}
    M82
    G90 
    M117 Printing...

[gcode_macro CANCEL_PRINT]
description: Cancel the current print
rename_existing: BASE_CANCEL_PRINT
gcode:
    M117 Print Cancelled
    G91                                           
    G1 Z10 F3000                  
    G90                        
    PARK_PURGE                  
    TURN_OFF_HEATERS
    M106 S0 
    SET_FAN_SPEED FAN=auxiliary_fan SPEED=0
    CLEAR_PAUSE
    BASE_CANCEL_PRINT
    M117 Ready

[gcode_macro PARK_PURGE]
description: Move the head to the purge bucket
gcode:
    {% if "xyz" not in printer.toolhead.homed_axes %}
        G28
    {% endif %}
    G90
    {% if printer.toolhead.position.z < 10 %}
        G1 Z10 F900       ; Lift Z slightly higher for safety
    {% endif %}
    G1 X10 Y-25 F6000     ; Updated location X10, Y-25                   

[adxl345]
axes_map: y, -x, z

[force_move]
enable_force_move: True
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

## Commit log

2025-05-13 Add base files
    [Configuration.h, Configuration_adv.h, esp32.csv]
2025-05-16 Add more models
    [8mm steel rod extrusion mount - Rev.1.0.stl, Z axis bearing stablizer mount - Rev.1.0.stl]
2025-05-18 Add torque curves
2025-06-18 Kinematics Update
    [30mm height psu support.stl, 4010 Shroud Rev.1.3.stl, 8mm Rod Extrusion Mount.stl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]
2025-07-22 Update 7-21-25
    [Configuration.h, Configuration_adv.h]
2025-07-26 v0.8 Update
    [15mm square tube cable clip (Epoxy Mounted).stl, 15mm square tube extrusion mount.stl, AC Plug + Power Switch extrusion mount.stl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]
2025-10-18 Chimera v1.5 Release - Part 2/2
    [4010 Shroud Rev.1.3.stl, 8mm Linear Bearing Extrusion Mount.stl, 8mm steel rod extrusion mount (Y-axis) - Rev.1.0.stl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]
2025-10-18 Readd files
    [15mm square tube cable clip (Epoxy Mounted).stl, 15mm square tube extrusion mount.stl, 30mm height psu support.stl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]
2025-10-18 Chimera v1.5
    [15mm square tube cable clip (Epoxy Mounted).stl, 15mm square tube extrusion mount.stl, 30mm height psu support.stl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]
2026-01-07 Chimera v2.0!
    [20mm Extrusion Vertical Cut Cover.stl, 4010 Shroud Rev.1.3.stl, 4010 Shroud.stl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]
2026-01-08 Create t-slot vfa.webp
2026-01-10 Chimera iXY v2.0!
    [8mm steel rod extrusion mount (OLD).stl, 8mm steel rod extrusion mount (Z-axis, Bottom & Top) - Rev.3.0.stl]
2026-01-10 Chimera iXY v2.0
    [Filament Guide - Bottom.stl, Filament Guide - Top.stl]

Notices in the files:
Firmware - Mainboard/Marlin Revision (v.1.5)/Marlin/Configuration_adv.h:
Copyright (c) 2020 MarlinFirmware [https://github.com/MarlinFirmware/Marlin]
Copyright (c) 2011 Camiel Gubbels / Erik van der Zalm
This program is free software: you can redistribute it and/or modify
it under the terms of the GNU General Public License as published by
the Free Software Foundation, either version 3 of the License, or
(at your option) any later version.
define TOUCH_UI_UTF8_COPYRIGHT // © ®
